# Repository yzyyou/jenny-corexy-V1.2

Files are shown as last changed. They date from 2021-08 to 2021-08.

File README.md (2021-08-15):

# jenny-corexy-V1.2
metallized structure inspire by vorondesign voron2.4 https://github.com/VoronDesign/Voron-2

Project Home  http://wiki.jenny3dprint.com/index.php?title=Jenny_corexy_voron_V1.2_mainpage
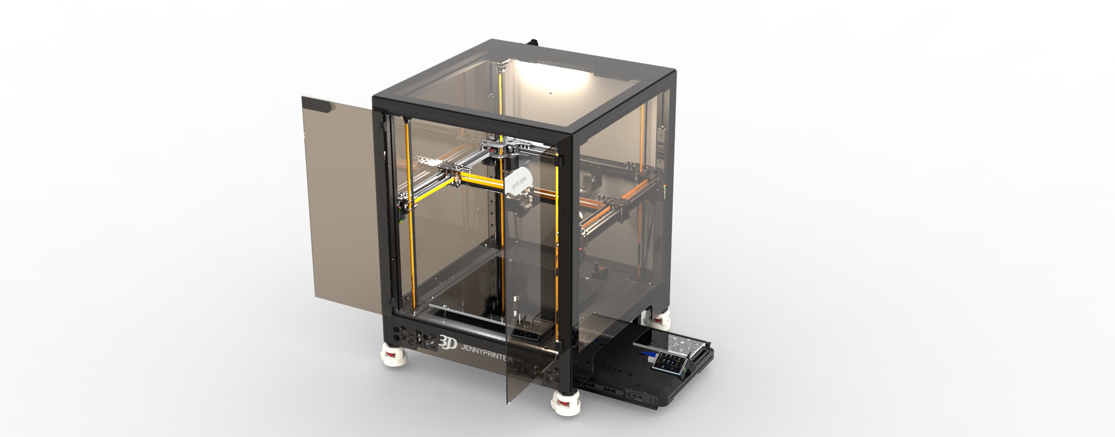
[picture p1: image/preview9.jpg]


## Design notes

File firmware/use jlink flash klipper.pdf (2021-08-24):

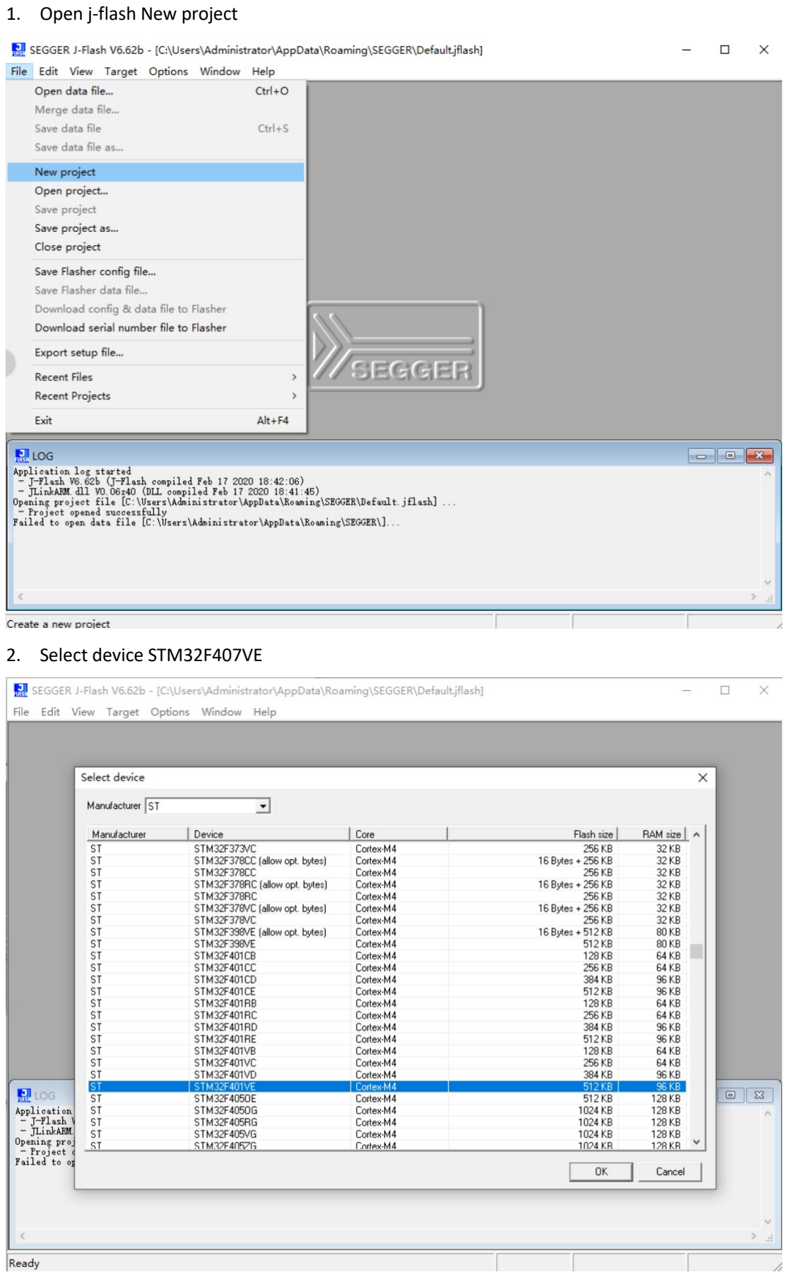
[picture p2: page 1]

### 1. Open j-flash New project

### 2. Select device STM32F407VE

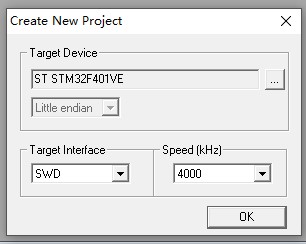
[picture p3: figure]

### 3. Open data file klipper.bin,start address use 0x8000000

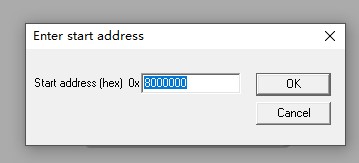
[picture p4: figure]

### 4. Use Jlink connect to MCU board’s SWDIO 、SWCLK 、GND、D+3V3

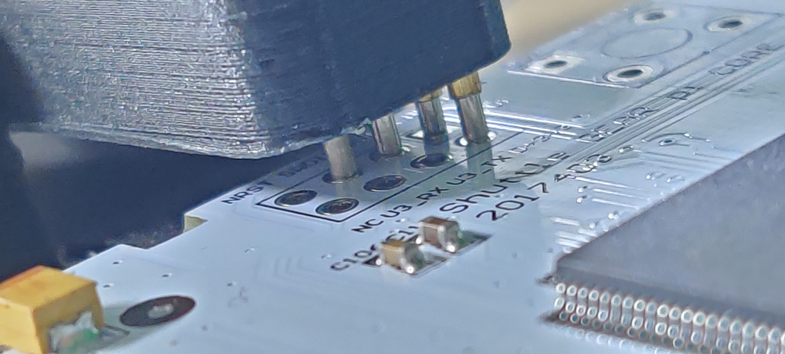
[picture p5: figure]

### 5. Click Target menu -> connect

### 6. Click Target menu -> Manua Programming -> Erase chip

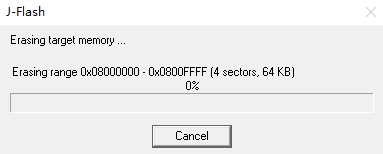
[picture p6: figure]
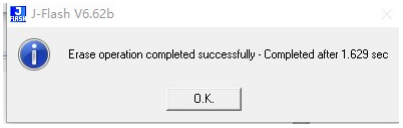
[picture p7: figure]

### 7. Click Target menu -> Manua Programming -> Program & Verify

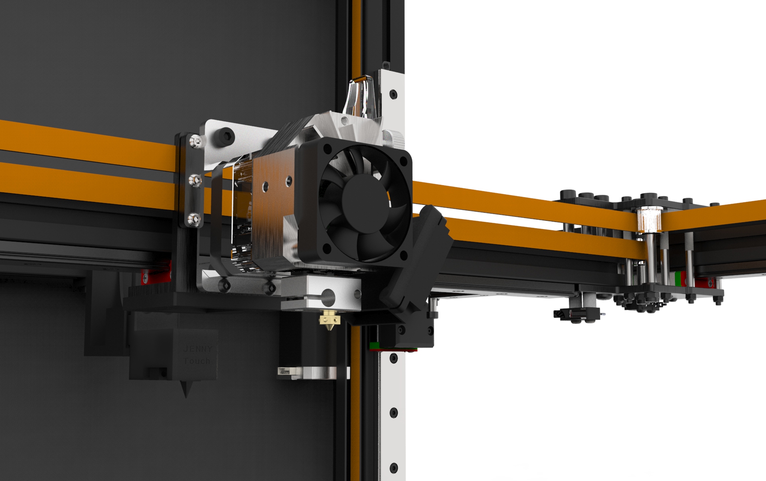
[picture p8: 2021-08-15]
image/preview7.jpg

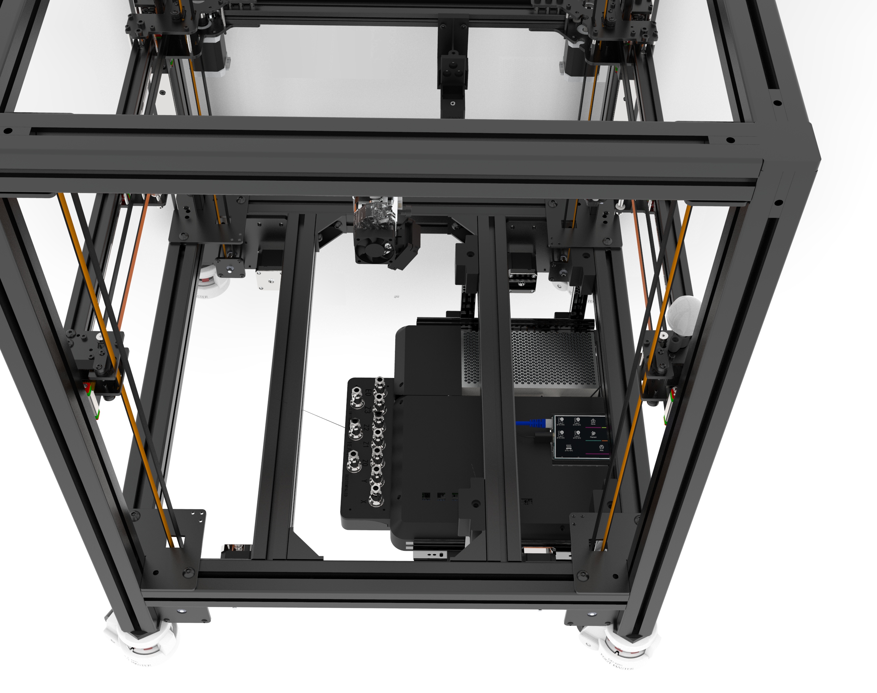
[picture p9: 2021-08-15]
image/preview3.jpg

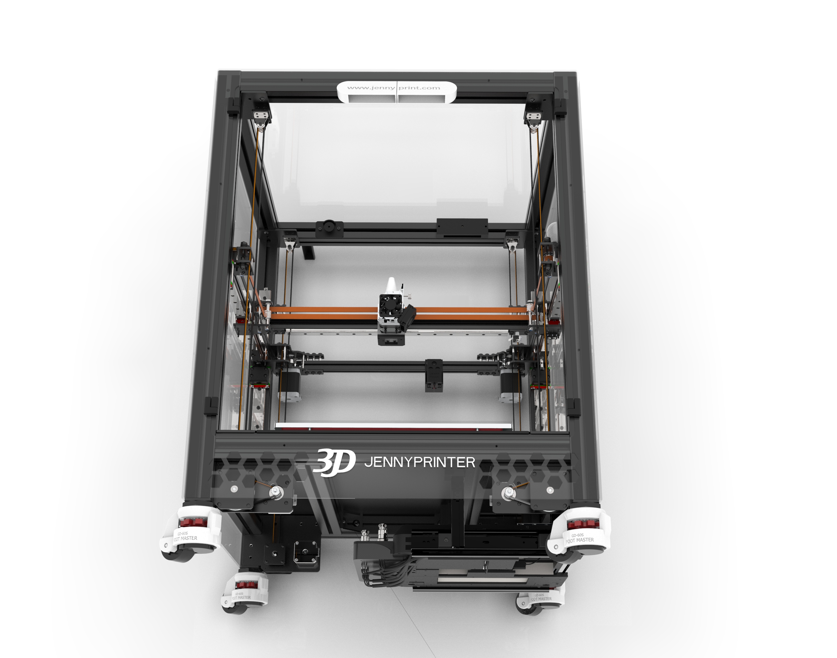
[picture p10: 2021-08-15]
image/preview4.jpg

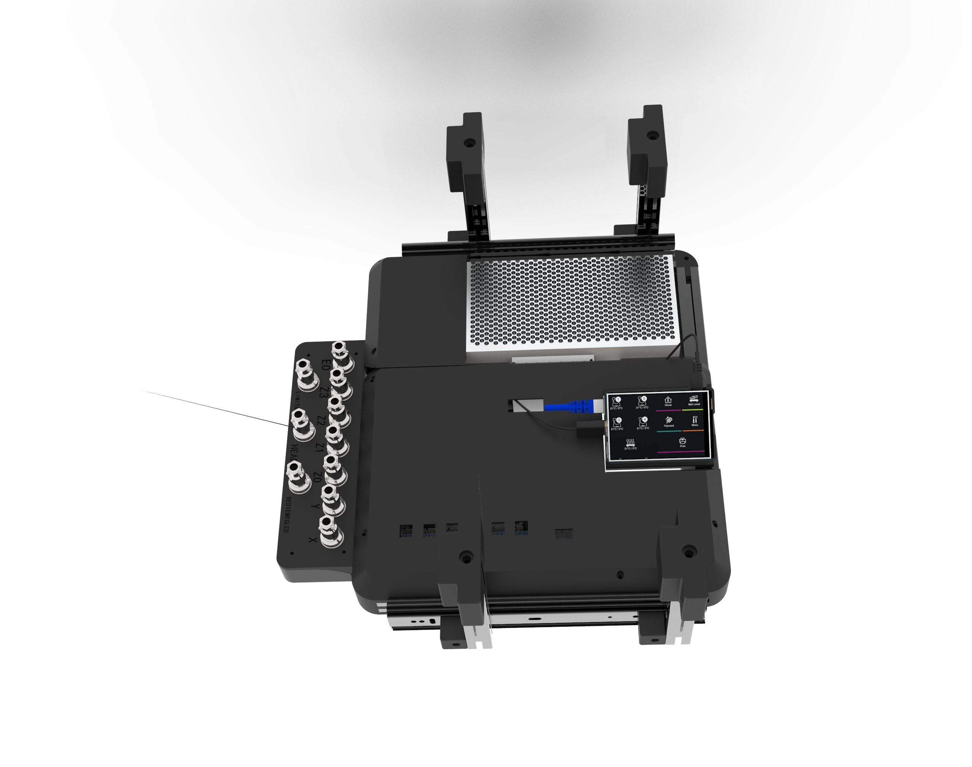
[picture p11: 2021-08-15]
image/preview8.jpg

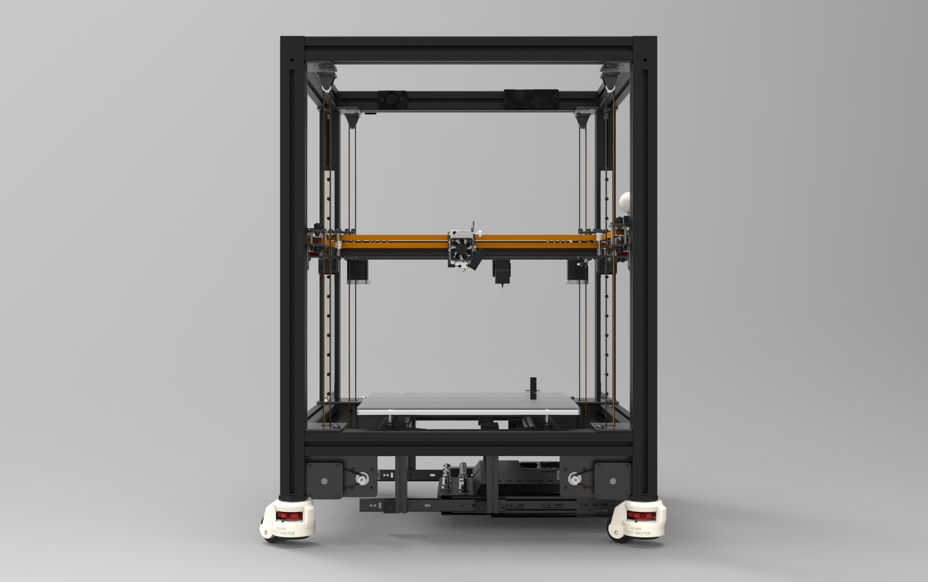
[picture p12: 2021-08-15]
image/preview2.jpg

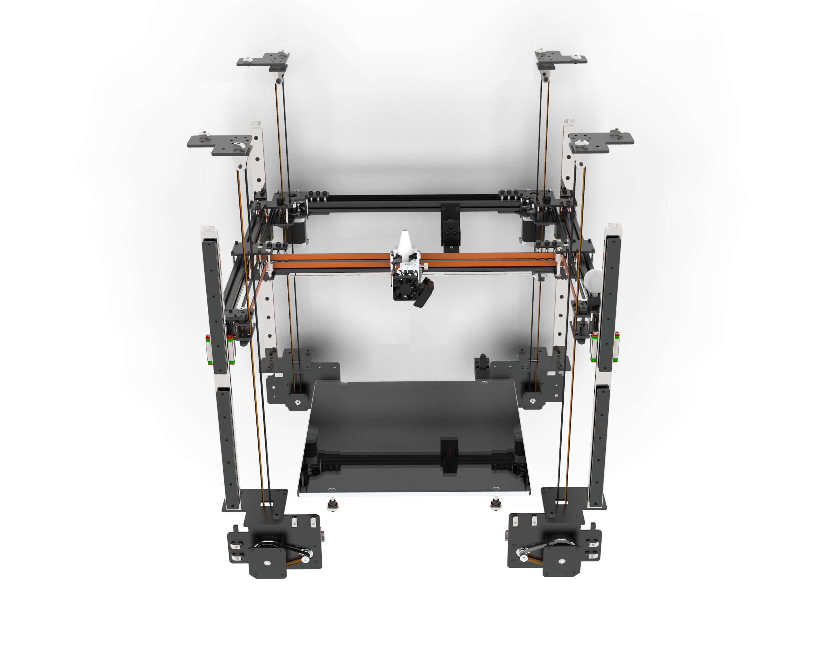
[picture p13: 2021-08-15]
image/preview6.jpg

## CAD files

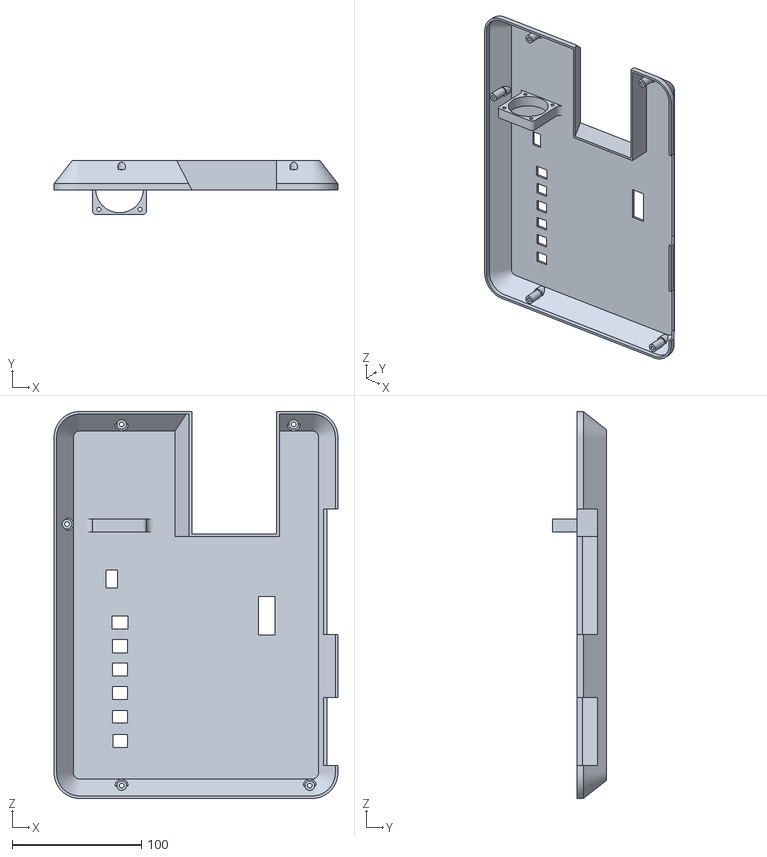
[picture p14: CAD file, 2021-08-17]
STLs/8_(optional)Main board cover plate.STL
220.0 x 42.0 x 300.0

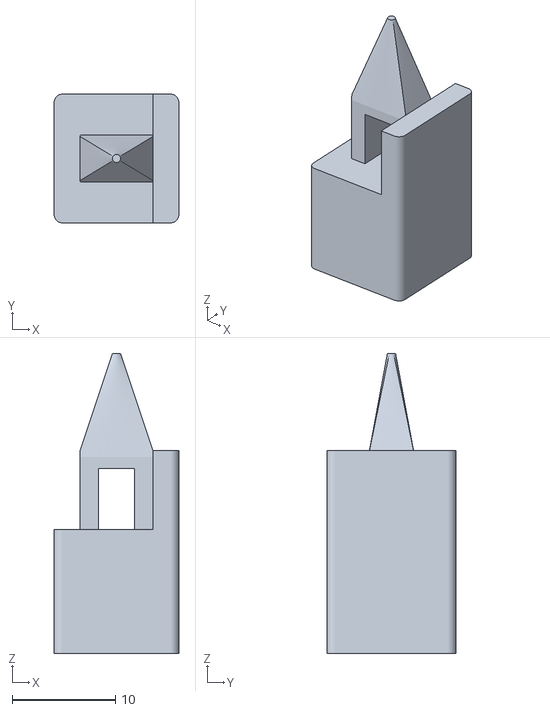
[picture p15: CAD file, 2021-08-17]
STLs/21_JennyTouch centre.STL
12.1 x 12.4 x 29.0

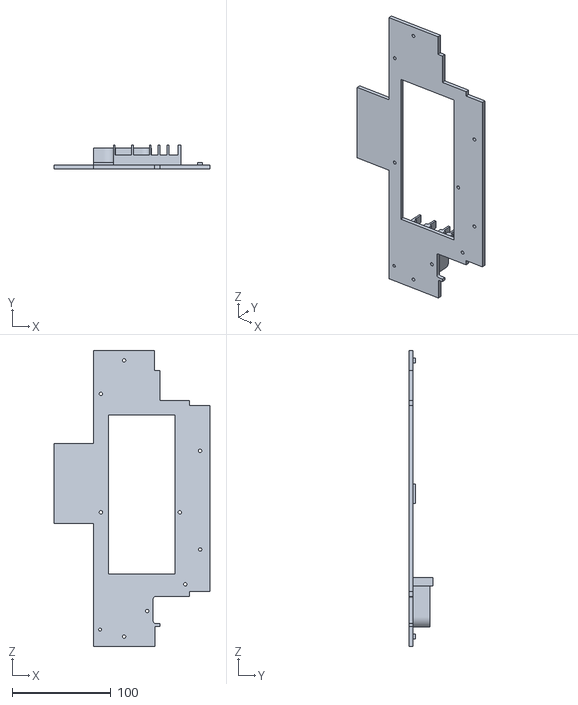
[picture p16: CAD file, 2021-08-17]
STLs/9_(optional)power bracket.STL
158.0 x 24.0 x 300.0

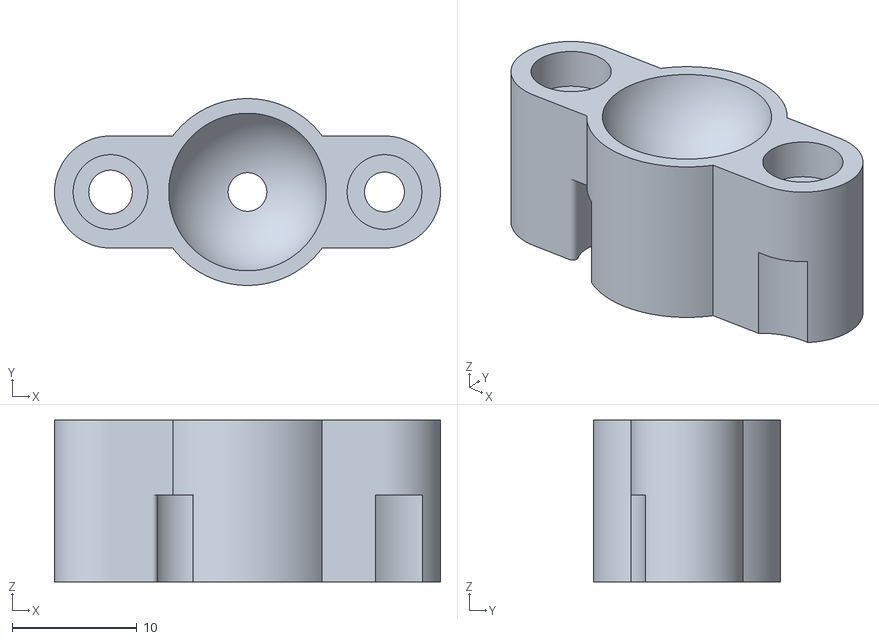
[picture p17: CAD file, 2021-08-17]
STLs/4_USB camera bracket.STL
31.0 x 15.0 x 13.0

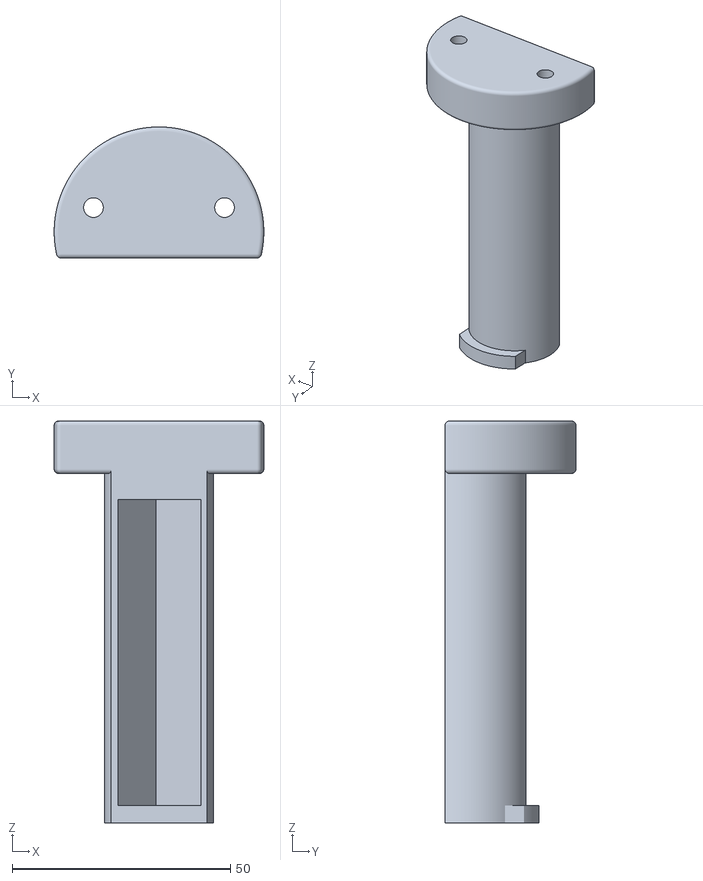
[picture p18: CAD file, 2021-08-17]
STLs/11_Filament hanging.STL
48.0 x 30.0 x 92.0

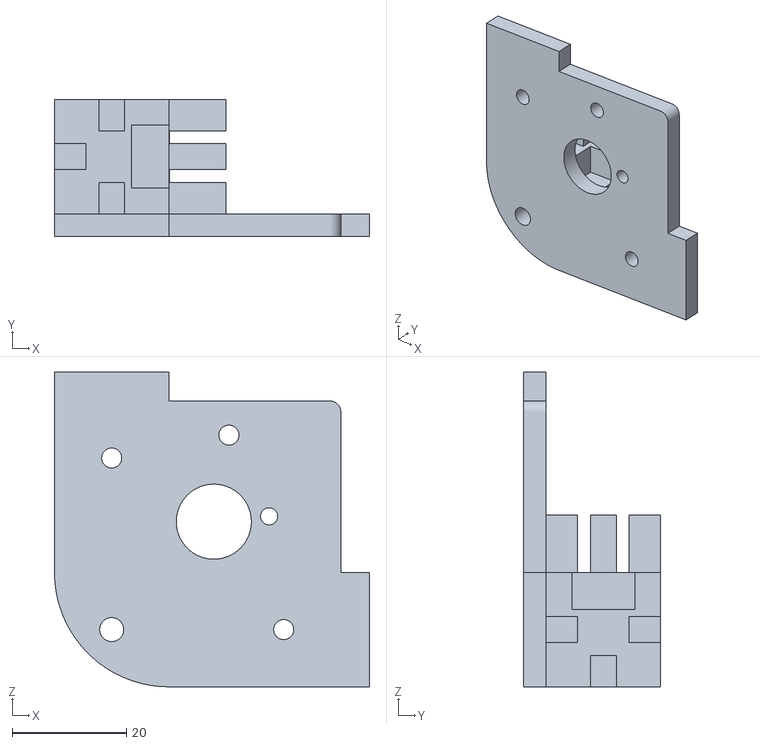
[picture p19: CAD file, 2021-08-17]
STLs/6_(optional)drawer cornerx4.STL
55.1 x 24.0 x 55.0

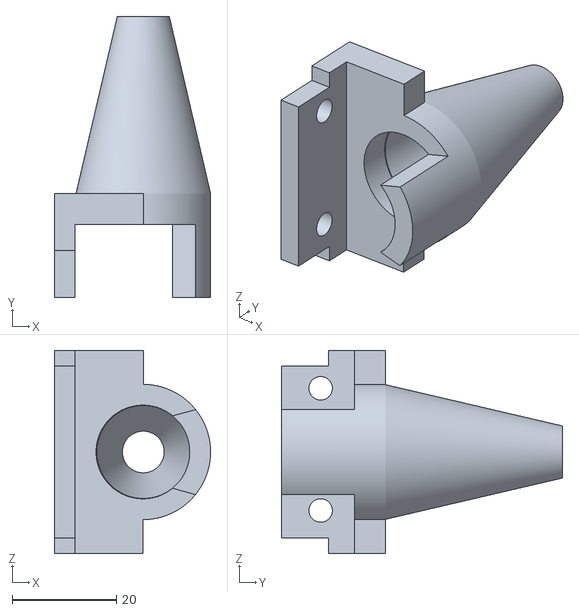
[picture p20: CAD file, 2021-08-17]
STLs/27_BMG Printhead wireTPU print.STL
30.0 x 54.0 x 39.0

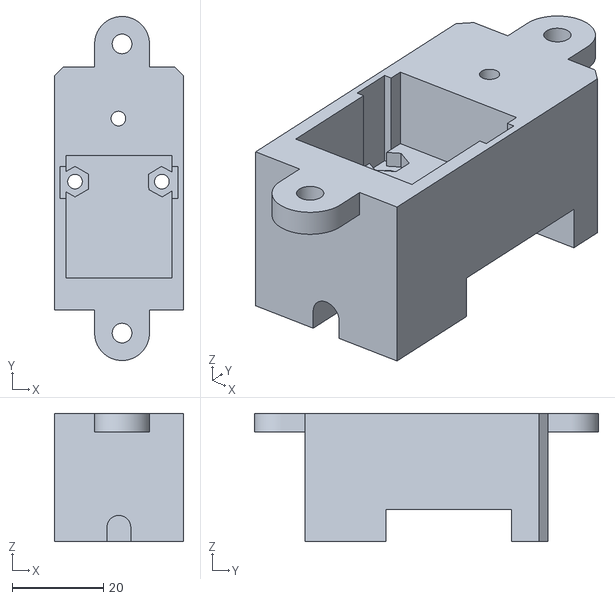
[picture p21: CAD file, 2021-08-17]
STLs/20_JennyLimitSwitch body.STL
28.3 x 75.2 x 28.0

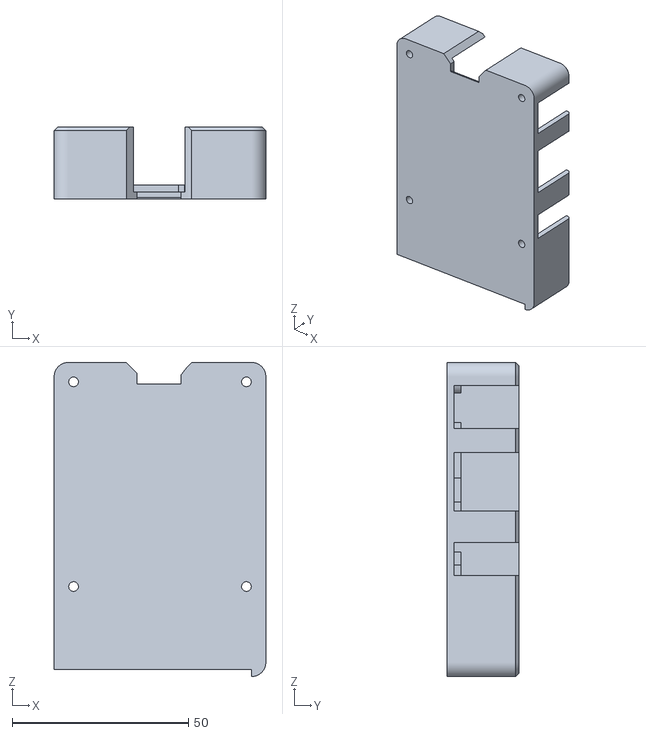
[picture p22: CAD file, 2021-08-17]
STLs/18_(optional)raspberry pi cover.STL
60.0 x 20.5 x 89.0

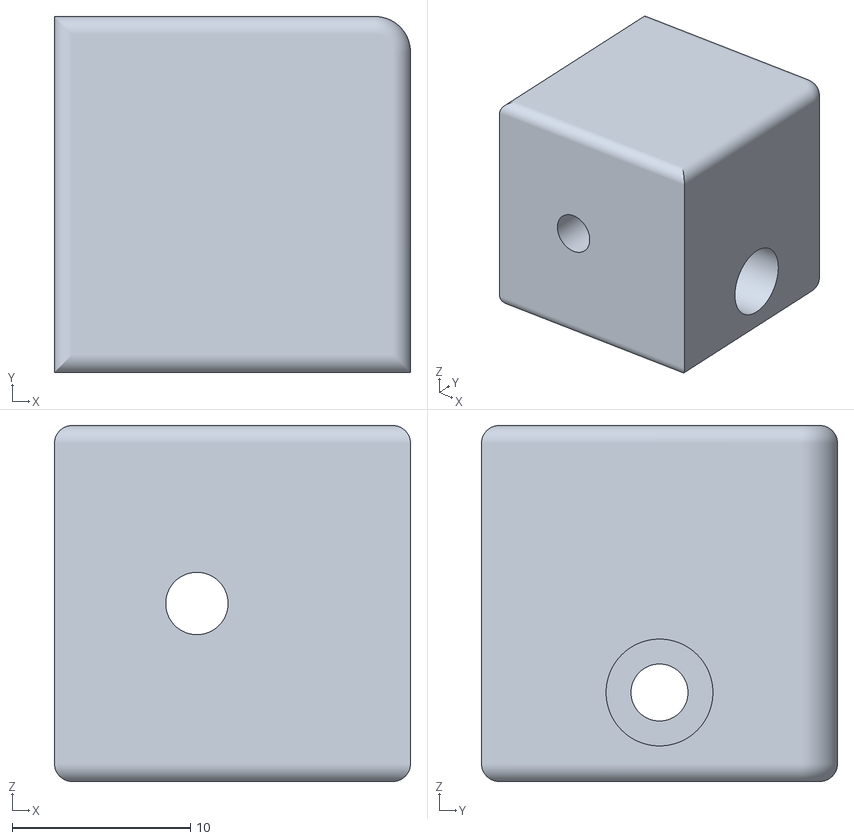
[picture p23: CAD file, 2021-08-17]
STLs/7_Drawer fixation cubex4.STL
20.0 x 20.0 x 20.0

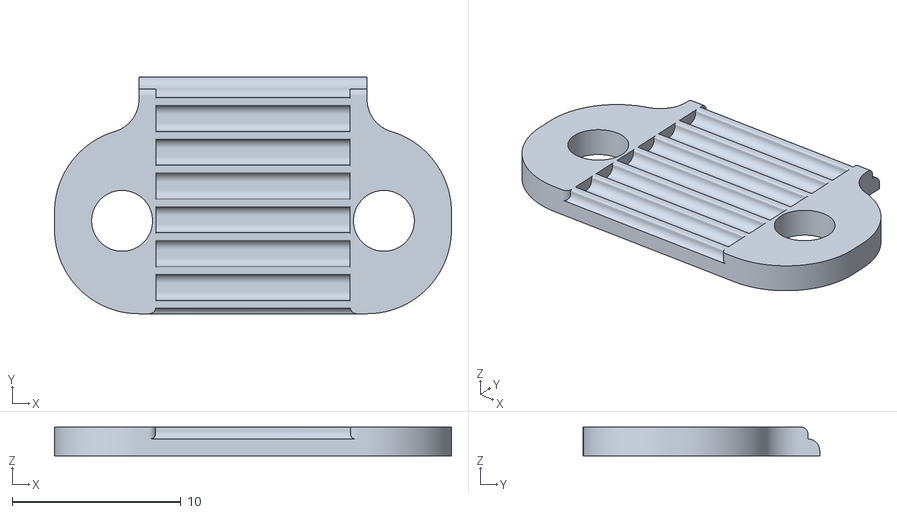
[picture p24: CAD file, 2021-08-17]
STLs/14_Z blet block bottom x8.STL
23.5 x 14.0 x 1.70

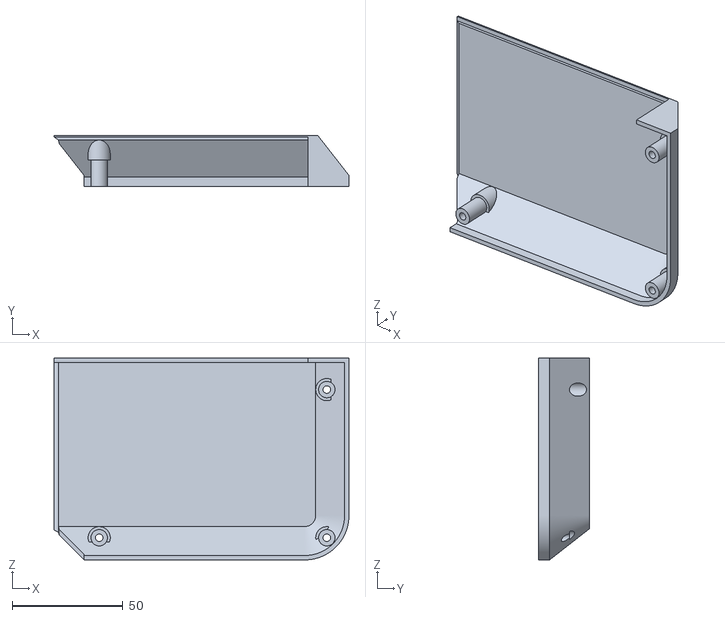
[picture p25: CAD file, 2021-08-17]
STLs/16_(optional)power cover.STL
133.0 x 23.0 x 91.0

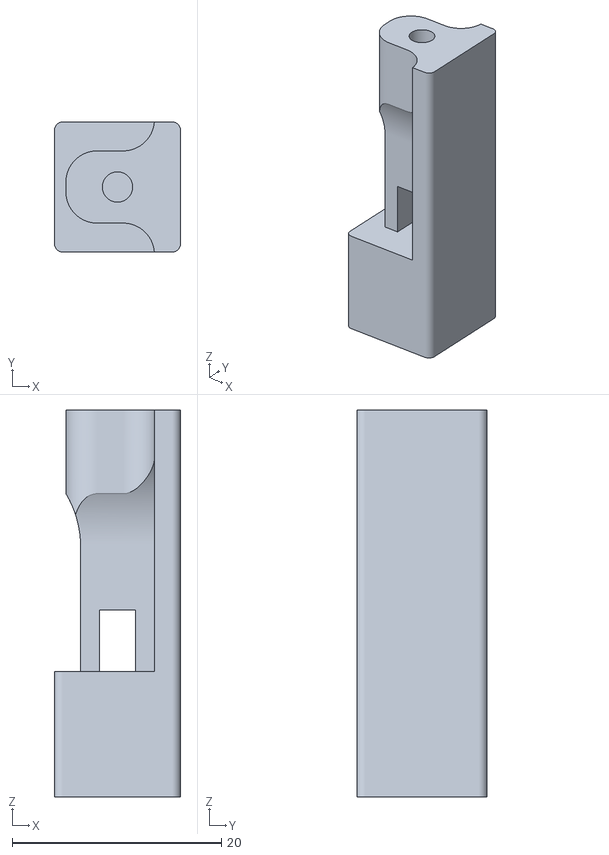
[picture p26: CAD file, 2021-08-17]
STLs/19_JennyLimitSwitch centre.STL
12.1 x 12.4 x 37.0

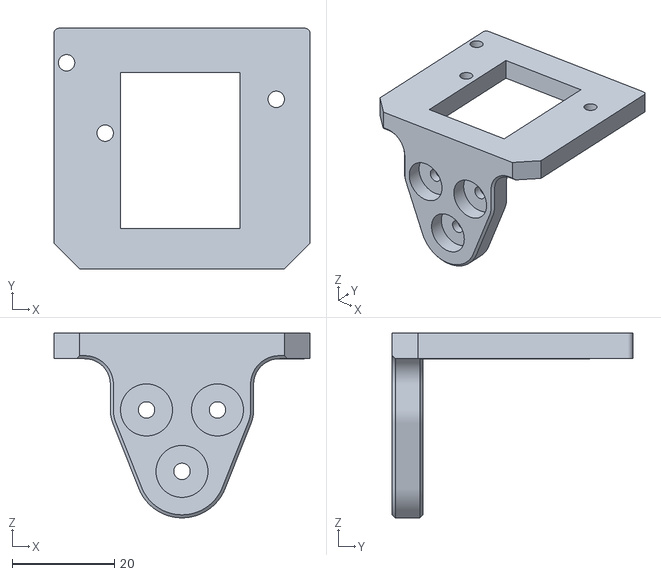
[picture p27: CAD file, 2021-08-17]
STLs/23_JennyTouch bracket.STL
50.0 x 47.0 x 36.1

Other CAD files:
Panels/jenny corexy Panels(350x350x400).dwg
Panels/jenny corexy Panels(410x410x400).dwg
STLs/3_(optional)ssr bracket.STL
STLs/1_Gantry linear rails blockx4.STL
STLs/10_printhed fan bracket.STL
STLs/12_(optional)aviation plug cover.STL
STLs/13_(optional)aviation plug bottom.STL
STLs/15_Z blet block top x8.STL
STLs/17_(optional)raspberry pi bracket.STL
STLs/1_(optional)Gantry linear rails block(standby)x4.STL
STLs/22_JennyTouch mount.STL
STLs/24_JennyTouch body.STL
STLs/26_printhead buckle.STL
STLs/2_(optional)SEMotherboard bracket.STL
STLs/5_ Drawer fixation doppx4.STL

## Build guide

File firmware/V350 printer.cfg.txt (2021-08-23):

[include kiauh_macros.cfg]
[mcu]
serial:  /dev/ttyUSB0
restart_method: command

#[menu __main __octoprint]
#type: disabled

[pause_resume]

[display_status]

[virtual_sdcard]
path: ~/gcode_files

[printer]
kinematics: corexy
max_velocity: 250
max_accel: 6000
#max_accel_to_decel : 7000
max_z_velocity: 60
max_z_accel: 600

[stepper_x]
step_pin: PB2
dir_pin: !PA0
enable_pin: !PE2
step_distance: 0.0125
endstop_pin: !PD12
position_endstop: 350
position_max: 350
homing_speed: 190
homing_retract_dist: 0

[stepper_y]
step_pin: PC14
dir_pin: !PE6
enable_pin: !PC15
step_distance: 0.0125
endstop_pin: !PA11
position_endstop: 350
position_max: 350
homing_speed: 190
homing_retract_dist: 0

## Z0 Stepper - Front Left
[stepper_z]
step_pin: PE5
dir_pin: !PE4
enable_pin: !PC13
step_distance: 0.00125
endstop_pin: !PE1
position_endstop: 3.9 #modfiy this when nozzle changed.more small more far.
position_max: 350
homing_speed: 20
position_min: -10.0
second_homing_speed: 3.0
homing_retract_dist: 3.0

##      Z1 Stepper - Rear Left
[stepper_z1]
step_pin: PA1
dir_pin: PB0
enable_pin: !PC5
step_distance: 0.00125

##      Z2 Stepper - Rear Right
[stepper_z2]
step_pin: PC4
dir_pin: !PE3
enable_pin: !PB1
step_distance: 0.00125

##      Z3 Stepper - Front Right
[stepper_z3]
step_pin: PB3 
dir_pin: PB4
enable_pin: !PB5
#step_distance: 0.0015625
step_distance: 0.00125

[extruder]
## STP -> step pin
step_pin: PE8
## FR -> dir pin
dir_pin: PE7
## ST -> enable pin
enable_pin: !PE9
#step_distance: .00194
step_distance: .0048
nozzle_diameter: 0.400
filament_diameter: 1.750
heater_pin: !PC6 # Heat0
sensor_pin:  PC0 # T1 Header
#sensor_type: PT100 INA826
sensor_type: EPCOS 100K B57560G104F
control: pid
#pid_Kp=17.186 pid_Ki=0.556 pid_Kd=132.761
pid_Kp: 23.034
pid_Ki: 0.704
pid_Kd: 188.3
min_temp: -20
max_temp: 350
max_extrude_cross_section:100
##      Try to keep pressure_advance below 1.0
pressure_advance: 0.046
##      Default is 0.040, leave stock
pressure_advance_smooth_time: 0.040
max_extrude_only_velocity:100
max_extrude_only_accel:3000

[verify_heater extruder]
#max_error: 120
#   The maximum "cumulative temperature error" before raising an
#   error. Smaller values result in stricter checking and larger
#   values allow for more time before an error is reported.
#   Specifically, the temperature is inspected once a second and if it
#   is close to the target temperature then an internal "error
#   counter" is reset; otherwise, if the temperature is below the
#   target range then the counter is increased by the amount the
#   reported temperature differs from that range. Should the counter
#   exceed this "max_error" then an error is raised. The default is
#   120.
#check_gain_time: 15
#   This controls heater verification during initial heating. Smaller
#   values result in stricter checking and larger values allow for
#   more time before an error is reported. Specifically, during
#   initial heating, as long as the heater increases in temperature
#   within this time frame (specified in seconds) then the internal
#   "error counter" is reset. The default is 20 seconds for extruders
#   and 60 seconds for heater_bed.
#hysteresis: 3
#   The maximum temperature difference (in Celsius) to a target
#   temperature that is considered in range of the target. This
#   controls the max_error range check. It is rare to customize this
#   value. The default is 5.
#heating_gain: 6
#   The minimum temperature (in Celsius) that the heater must increase
#   by during the check_gain_time check. It is rare to customize this
#   value. The default is 2.

[heater_bed]
heater_pin: !PB13
sensor_pin: PC1
##      Thermistor Types
##   "EPCOS 100K B57560G104F"
##   "ATC Semitec 104GT-2"
##   "NTC 100K beta 3950"
##   "Honeywell 100K 135-104LAG-J01"
##   "NTC 100K MGB18-104F39050L32" (Keenovo Heater Pad)
##   "AD595"
##   "PT100 INA826"
sensor_type: EPCOS 100K B57560G104F
control: watermark
min_temp: 0
max_temp: 120

[probe]
pin: PC8
x_offset: 0
y_offset: 25.0
z_offset: 0
speed: 10.0
samples: 2
samples_result: average
sample_retract_dist: 3.0
samples_tolerance: 0.05
samples_tolerance_retries: 3

[fan]
pin: !PB6
kick_start_time: 0.5
off_below: 0.10
cycle_time: 0.001

[heater_fan fan1]
pin: !PB8
max_power: 1.0
kick_start_time: 0.5
heater: extruder
heater_temp: 50.0

[heater_fan controller_fan]
pin: !PB9
kick_start_time: 0.500
heater: heater_bed
heater_temp: 45.0

#[heater_fan exhaust_fan]
#pin: z:P2.7
#max_power: 1.0
#shutdown_speed: 0.0
#kick_start_time: 5.0
#heater: heater_bed
#heater_temp: 60
#fan_speed: 1.0

#[heater_fan fan2]
#pin: PE6

[skew_correction]

#[idle_timeout]
#timeout: 1800

[force_move]
enable_force_move: true
#   Set to true to enable FORCE_MOVE and SET_KINEMATIC_POSITION
#   extended G-Code commands. The default is false.

[homing_override]
axes: z
set_position_z: 0
gcode:
   SET_PIN PIN=Z_ENABLE VALUE=100
   G90
   G0 Z50 F1200
   G28 X Y 
   G0 X280 Y320 F4800
   G28 Z
   G0 Z50 F1200
   G0 X240  F4800

[quad_gantry_level]
gantry_corners:
        -60,-10
        340,360
#       Probe points
points:
	10,10
	10,270
	310,270
        310,10	
speed: 80
horizontal_move_z:35
retries: 5
retry_tolerance: 0.04
max_adjust: 90

#####################################################################
#       Macros
#####################################################################
[output_pin case_light]
pin: !PA3
pwm: true
shutdown_value: 0
cycle_time: 0.01
scale: 255

[output_pin Z_ENABLE]
pin: !PC7
pwm: true
shutdown_value: 0
cycle_time: 0.01
scale: 100

[gcode_button POWER_OFF_KEY]
pin:PA15
press_gcode:
        SET_PIN PIN=POWER_OFF VALUE=100

[output_pin POWER_OFF]
#pin: !PA15
pin: !PB12
pwm: true
shutdown_value: 0
cycle_time: 0.01
scale: 100

[gcode_macro M355]
variable_light_before: 0
default_parameter_S: 0
default_parameter_P: 0
gcode:
        SET_PIN PIN=case_light VALUE={S|float * P|float}

[gcode_macro ENDSTOPS_PROBE_STATUS]
gcode:
        QUERY_ENDSTOPS
        QUERY_PROBE

[gcode_macro TEST_X]
gcode:        
        STEPPER_BUZZ STEPPER=stepper_x 

[gcode_macro TEST_Y]
gcode:        
        STEPPER_BUZZ STEPPER=stepper_y 

[gcode_macro TEST_Z0]
gcode:   
        STEPPER_BUZZ STEPPER=stepper_z

[gcode_macro TEST_Z1]
gcode:   
        STEPPER_BUZZ STEPPER=stepper_z1

[gcode_macro TEST_Z2]
gcode:   
        STEPPER_BUZZ STEPPER=stepper_z2

[gcode_macro TEST_Z3]
gcode:   
        STEPPER_BUZZ STEPPER=stepper_z3

[gcode_macro LIGHT_ON]
gcode:
        M355 S1 P255

[gcode_macro LIGHT_OFF]
gcode:
        M355 S0 P0

[gcode_macro MOUNT_PROBE]
gcode:
        G1 X220 Y300 F3600;
        G1 X220 Y350 F3600;
        G1 X180 Y350 F3600;
        G1 X180 Y300 F3600;

[gcode_macro UMOUNT_PROBE]
gcode:
        G1 X180 Y300 F3600;
        G1 X180 Y350 F3600;
        G1 X220 Y350 F3600;
        G1 X220 Y300 F3600;

[gcode_macro UNLOCK_Z_MOVE]
gcode:
        SET_PIN PIN=Z_ENABLE VALUE=100

[gcode_macro ENABLE_Z_MOVE]
gcode:        
        SET_STEPPER_ENABLE STEPPER=stepper_z ENABLE=1
        SET_STEPPER_ENABLE STEPPER=stepper_z1 ENABLE=1
        SET_STEPPER_ENABLE STEPPER=stepper_z2 ENABLE=1
        SET_STEPPER_ENABLE STEPPER=stepper_z3 ENABLE=1
        SET_PIN PIN=Z_ENABLE VALUE=100

[gcode_macro FORCE_POWER_OFF]
gcode:
        SET_PIN PIN=POWER_OFF VALUE=100

[gcode_macro G32]
gcode:
    #BED_MESH_CLEAR
    G28
    MOUNT_PROBE
    QUAD_GANTRY_LEVEL
    UMOUNT_PROBE
    G28
    G0 X250 Y250 Z20 F1200

[gcode_macro POWER_LOSS]
description: in the actual running print power loss happen
gcode:
    
    SET_PIN PIN=case_light VALUE=0.00 SAVE=0
    #SET_FAN_SPEED controller_fan=0
    #SET_FAN_SPEED fan=0
    #SET_FAN_SPEED fan1=0
    M106 S0
    #################
    ##### set defaults #####
    #{% set x = params.X|default(230) %}      #edit to your park position
    #{% set y = params.Y|default(230) %}      #edit to your park position
    #{% set z = params.Z|default(10)|float %} #edit to your park position
    #{% set e = params.E|default(1) %}        #edit to your retract length
    ##### calculate save lift position #####
  
    #{%set min_extrude_temp = printer.configfile.settings["extruder"]["min_extrude_temp"]|int %}
    #{%set act_extrude_temp = printer.extruder.temperature|int %}
    
    #SAVE_GCODE_STATE NAME=PAUSE_state

    PAUSE
    TURN_OFF_HEATERS
    ##### end of definitions #####

    M117 unexpected power off happened

[gcode_macro PRINT_START]
#   Use PRINT_START for the slicer starting script - please customise for your slicer of choice
gcode:
    SET_SKEW XY=140.6,140.8,99.94
    #G28                            ; home all axes
    G32
    G1 Z20 F3000                   ; move nozzle away from bed
    G1 X30 Y0 Z0.3 F3000
    G92 E0
    G1 X40 E20 F100
    G1 X50 F2100
    G92 E0

[gcode_macro PRINT_END]
#   Use PRINT_END for the slicer ending script - please customise for your slicer of choice
gcode:
    M400                           ; wait for buffer to clear
    G92 E0                         ; zero the extruder
    G1 E-10.0 F3600                ; retract filament
    G91                            ; relative positioning
    G0 Z1.00 X20.0 Y25.0 F20000    ; move nozzle to remove stringing
    TURN_OFF_HEATERS
    M107                           ; turn off fan
    G1 Z2 F3000                    ; move nozzle up 2mm
    G90                            ; absolute positioning
    G0  X125 Y250 F3600            ; park nozzle at rear
    SET_SKEW CLEAR=1

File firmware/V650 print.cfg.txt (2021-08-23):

[include kiauh_macros.cfg]
[mcu]
serial:  /dev/ttyUSB0
restart_method: command

#[menu __main __octoprint]
#type: disabled

#[mcu rpi]
#serial: /tmp/klipper_host_mcu

#[adxl345]
#cs_pin: rpi:gpio11

#[resonance_tester]
#accel_chip: adxl345
#probe_points:
#    325,325,20  # middle of print bed

[pause_resume]

[display_status]

[virtual_sdcard]
path: ~/gcode_files

[printer]
kinematics: corexy
max_velocity: 260
max_accel:6000
#max_accel_to_decel:7000
max_z_velocity: 10
max_z_accel: 100

[stepper_x]
step_pin: PB2
dir_pin: !PA0
enable_pin: !PE2
step_distance: 0.0125
endstop_pin: PA11
position_endstop: 650
position_max: 650
homing_speed: 100
homing_retract_dist: 0

[stepper_y]
step_pin: PC14
dir_pin: !PE6
enable_pin: !PC15
step_distance: 0.0125
endstop_pin: PD12
position_endstop: 650
position_max: 650
homing_speed: 100
homing_retract_dist: 0

## Z0 Stepper - Front Left
[stepper_z]
step_pin: PE5
dir_pin: PE4
enable_pin: !PC13
step_distance: 0.0025
endstop_pin: PE0
position_endstop: 12.7 #modfiy this when nozzle changed.more small more far.
position_max: 512
homing_speed: 15
position_min: -10
second_homing_speed: 3.0
homing_retract_dist: 3.0

##      Z1 Stepper - Rear Left
[stepper_z1]
step_pin: PA1
dir_pin: !PB0
enable_pin: !PC5
step_distance: 0.0025

##      Z2 Stepper - Rear Right
[stepper_z2]
step_pin: PC4
dir_pin: PE3
enable_pin: !PB1
step_distance: 0.0025

##      Z3 Stepper - Front Right
[stepper_z3]
step_pin: PB3
dir_pin: !PB4
enable_pin: !PB5
#step_distance: 0.0015625
step_distance: 0.0025

[extruder]
step_pin: PE8
dir_pin: PE7
enable_pin: !PE9
#step_distance: .00194
step_distance: .0048
nozzle_diameter: 0.400
filament_diameter: 1.750
heater_pin: !PC6 # Heat0
sensor_pin:  PC0 # T1 Header
#sensor_type: PT100 INA826
sensor_type: EPCOS 100K B57560G104F
control: pid
#pid_Kp=17.186 pid_Ki=0.556 pid_Kd=132.761
#pid_Kp: 22.2
#pid_Ki: 1.08
#pid_Kd: 114
pid_Kp=18.731
pid_Ki=0.827 
pid_Kd=106.065 

min_temp: -20
max_temp: 350
max_extrude_cross_section:100
##      Try to keep pressure_advance below 1.0
pressure_advance: 0.046
##      Default is 0.040, leave stock
pressure_advance_smooth_time: 0.040
max_extrude_only_velocity:100
max_extrude_only_accel:3000

[verify_heater extruder]
#max_error: 120
#   The maximum "cumulative temperature error" before raising an
#   error. Smaller values result in stricter checking and larger
#   values allow for more time before an error is reported.
#   Specifically, the temperature is inspected once a second and if it
#   is close to the target temperature then an internal "error
#   counter" is reset; otherwise, if the temperature is below the
#   target range then the counter is increased by the amount the
#   reported temperature differs from that range. Should the counter
#   exceed this "max_error" then an error is raised. The default is
#   120.
#check_gain_time: 15
#   This controls heater verification during initial heating. Smaller
#   values result in stricter checking and larger values allow for
#   more time before an error is reported. Specifically, during
#   initial heating, as long as the heater increases in temperature
#   within this time frame (specified in seconds) then the internal
#   "error counter" is reset. The default is 20 seconds for extruders
#   and 60 seconds for heater_bed.
#hysteresis: 3
#   The maximum temperature difference (in Celsius) to a target
#   temperature that is considered in range of the target. This
#   controls the max_error range check. It is rare to customize this
#   value. The default is 5.
#heating_gain: 6
#   The minimum temperature (in Celsius) that the heater must increase
#   by during the check_gain_time check. It is rare to customize this
#   value. The default is 2.

[heater_bed]
heater_pin: !PB13
sensor_pin: PC1
##      Thermistor Types
##   "EPCOS 100K B57560G104F"
##   "ATC Semitec 104GT-2"
##   "NTC 100K beta 3950"
##   "Honeywell 100K 135-104LAG-J01"
##   "NTC 100K MGB18-104F39050L32" (Keenovo Heater Pad)
##   "AD595"
##   "PT100 INA826"
sensor_type: EPCOS 100K B57560G104F
control: watermark
min_temp: 0
max_temp: 120

[probe]
pin: PC8
x_offset: 0
y_offset: 25.0
z_offset: 0
speed: 30.0
samples: 2
samples_result: average
sample_retract_dist: 3.0
samples_tolerance: 0.05
samples_tolerance_retries: 3

[fan]
pin: !PB8
kick_start_time: 0.5
off_below: 0.10
cycle_time: 0.001

[heater_fan fan1]
pin: !PB6
max_power: 1.0
kick_start_time: 0.5
heater: extruder
heater_temp: 50.0

[heater_fan controller_fan]
pin: !PB9
kick_start_time: 0.500
heater: heater_bed
heater_temp: 45.0

#[heater_fan exhaust_fan]
#pin: z:P2.7
#max_power: 1.0
#shutdown_speed: 0.0
#kick_start_time: 5.0
#heater: heater_bed
#heater_temp: 60
#fan_speed: 1.0

#[heater_fan fan2]
#pin: PE6

[skew_correction]
#SET_SKEW XY=140.5,140.1,99.92

#[idle_timeout]
#timeout: 1800

[force_move]
enable_force_move: true
#   Set to true to enable FORCE_MOVE and SET_KINEMATIC_POSITION
#   extended G-Code commands. The default is false.

[homing_override]
axes: z
set_position_z: 0
gcode:
   SET_PIN PIN=Z_ENABLE VALUE=100
   G90
   G0 Z50 F1200
   G28 X Y
   G0 X590 Y648  F4800
   G28 Z
   G0 Z50 F1200
   G0 X550  F4800

[quad_gantry_level]
gantry_corners:
        -60,-10
        750,800
#       Probe points
points:
        30,20
        30,560
        620,560
        620,20
speed: 100
horizontal_move_z: 50
retries: 5
retry_tolerance: 0.05
max_adjust: 90

#####################################################################
#       Macros
#####################################################################
[output_pin case_light]
pin: !PA3
pwm: true
shutdown_value: 0
cycle_time: 0.01
scale: 255

[output_pin Z_ENABLE]
pin: !PC7
pwm: true
shutdown_value: 0
cycle_time: 0.01
scale: 100

[gcode_button POWER_OFF_KEY]
pin:PA15
press_gcode:
        SET_PIN PIN=POWER_OFF VALUE=100

[output_pin POWER_OFF]
#pin: !PA15
pin: !PB12
pwm: true
shutdown_value: 0
cycle_time: 0.01
scale: 100

[gcode_macro M355]
variable_light_before: 0
default_parameter_S: 0
default_parameter_P: 0
gcode:
        SET_PIN PIN=case_light VALUE={S|float * P|float}

[gcode_macro ENDSTOPS_PROBE_STATUS]
gcode:
        QUERY_ENDSTOPS
        QUERY_PROBE

[gcode_macro TEST_X]
gcode:        
        STEPPER_BUZZ STEPPER=stepper_x 

[gcode_macro TEST_Y]
gcode:        
        STEPPER_BUZZ STEPPER=stepper_y 

[gcode_macro TEST_Z0]
gcode:   
        STEPPER_BUZZ STEPPER=stepper_z

[gcode_macro TEST_Z1]
gcode:   
        STEPPER_BUZZ STEPPER=stepper_z1

[gcode_macro TEST_Z2]
gcode:   
        STEPPER_BUZZ STEPPER=stepper_z2

[gcode_macro TEST_Z3]
gcode:   
        STEPPER_BUZZ STEPPER=stepper_z3

[gcode_macro LIGHT_ON]
gcode:
        M355 S1 P255

[gcode_macro LIGHT_OFF]
gcode:
        M355 S0 P0

[gcode_macro MOUNT_PROBE]
gcode:
        G1 X473 Y597 F3600;
        G1 X473 Y649 F3600;
        G1 X434 Y649 F3600;
        G1 X434 Y597 F3600;

[gcode_macro UMOUNT_PROBE]
gcode:
        G1 X434 Y597 F3600;
        G1 X434 Y647 F3600;
        G1 X473 Y647 F3600;
        G1 X473 Y597 F3600;

[gcode_macro UNLOCK_Z_MOVE]
gcode:
        SET_PIN PIN=Z_ENABLE VALUE=100

[gcode_macro ENABLE_Z_MOVE]
gcode:        
        SET_STEPPER_ENABLE STEPPER=stepper_z ENABLE=1
        SET_STEPPER_ENABLE STEPPER=stepper_z1 ENABLE=1
        SET_STEPPER_ENABLE STEPPER=stepper_z2 ENABLE=1
        SET_STEPPER_ENABLE STEPPER=stepper_z3 ENABLE=1
        SET_PIN PIN=Z_ENABLE VALUE=100

[gcode_macro FORCE_POWER_OFF]
gcode:
        SET_PIN PIN=POWER_OFF VALUE=100

[gcode_macro G32]
gcode:
    #BED_MESH_CLEAR
    G28
    MOUNT_PROBE
    QUAD_GANTRY_LEVEL
    UMOUNT_PROBE
    G28
    G0 X250 Y250 Z20 F1200

[gcode_macro POWER_LOSS]
description: in the actual running print power loss happen
gcode:
    
    SET_PIN PIN=case_light VALUE=0.00 SAVE=0
    #SET_FAN_SPEED controller_fan=0
    #SET_FAN_SPEED fan=0
    #SET_FAN_SPEED fan1=0
    M106 S0
    #################
    ##### set defaults #####
    #{% set x = params.X|default(230) %}      #edit to your park position
    #{% set y = params.Y|default(230) %}      #edit to your park position
    #{% set z = params.Z|default(10)|float %} #edit to your park position
    #{% set e = params.E|default(1) %}        #edit to your retract length
    ##### calculate save lift position #####
  
    #{%set min_extrude_temp = printer.configfile.settings["extruder"]["min_extrude_temp"]|int %}
    #{%set act_extrude_temp = printer.extruder.temperature|int %}
    
    #SAVE_GCODE_STATE NAME=PAUSE_state

    PAUSE
    TURN_OFF_HEATERS
    ##### end of definitions #####

    M117 unexpected power off happened

[gcode_macro PRINT_START]
#   Use PRINT_START for the slicer starting script - please customise for your slicer of choice
gcode:
    #G28                            ; home all axes
    SET_SKEW XY=140.5,140.1,99.92
    G32
    G1 Z20 F1200                   ; move nozzle away from bed
    G1 X30 Y10 Z0.3 F3600
    G92 E0
    G1 X40 E20 F100
    G1 X50 F2100
    G92 E0

[gcode_macro PRINT_END]
#   Use PRINT_END for the slicer ending script - please customise for your slicer of choice
gcode:
    M400                           ; wait for buffer to clear
    G92 E0                         ; zero the extruder
    G1 E-10.0 F3600                ; retract filament
    G91                            ; relative positioning
    G0 Z1.00 X20.0 Y25.0 F20000    ; move nozzle to remove stringing
    TURN_OFF_HEATERS
    M107                           ; turn off fan
    G1 Z8 F3000                    ; move nozzle up 2mm
    G90                            ; absolute positioning
    G0  X125 Y250 F3600            ; park nozzle at rear
    SET_SKEW CLEAR=1

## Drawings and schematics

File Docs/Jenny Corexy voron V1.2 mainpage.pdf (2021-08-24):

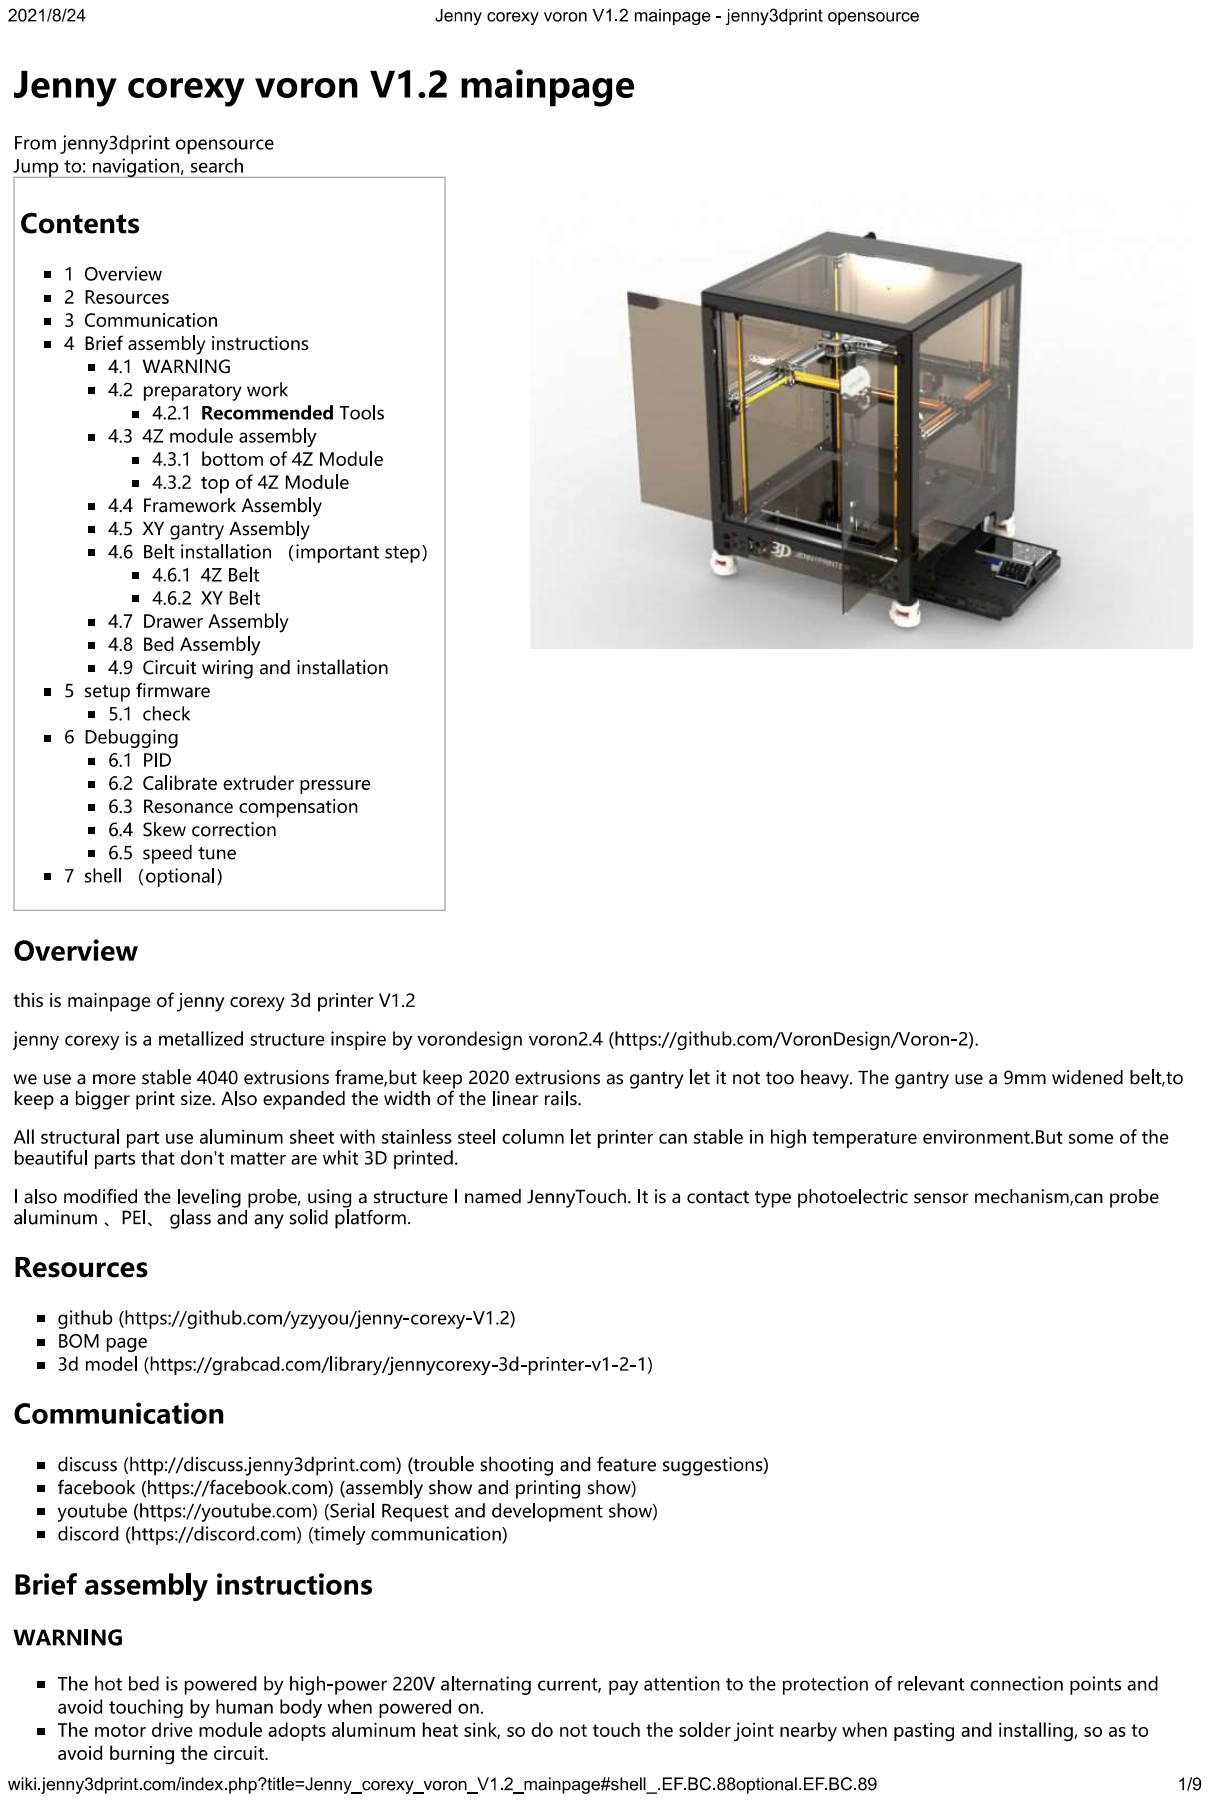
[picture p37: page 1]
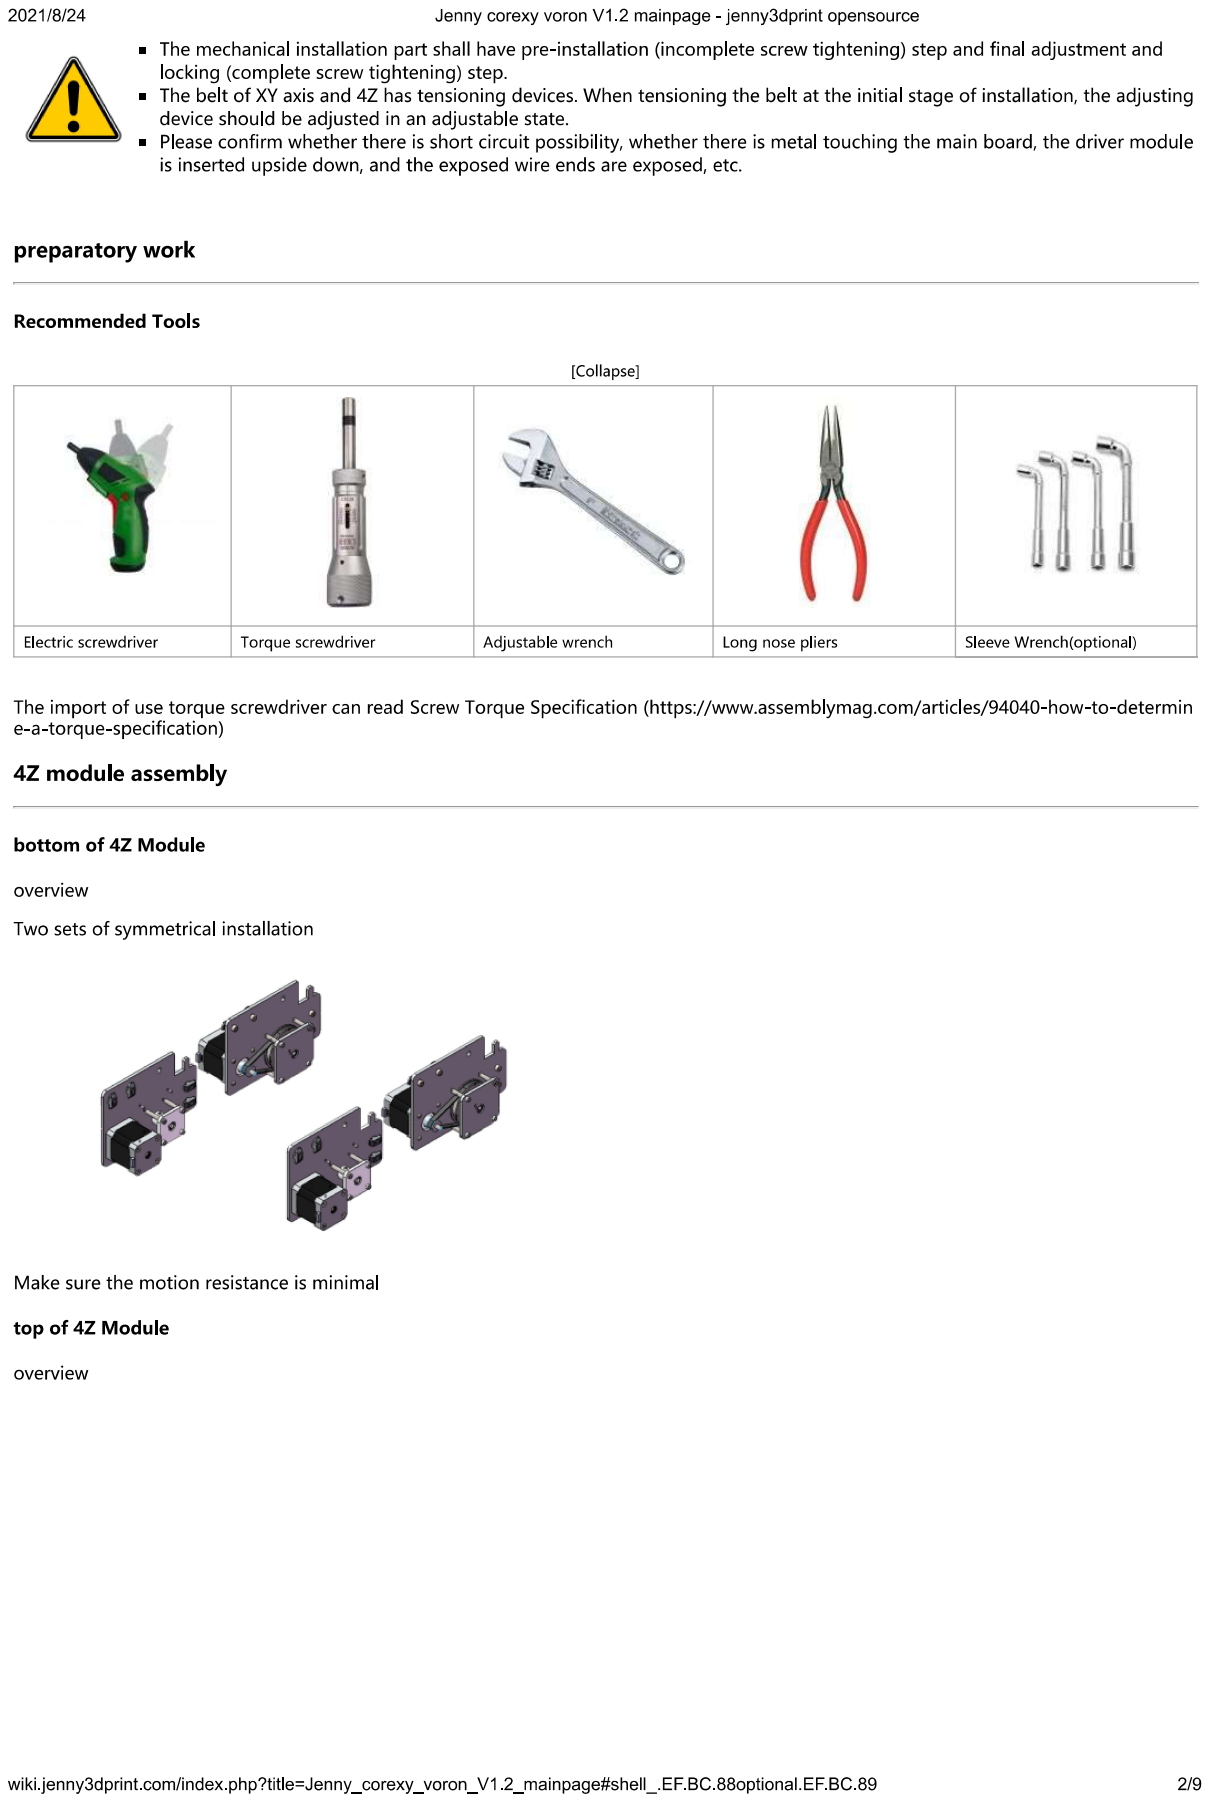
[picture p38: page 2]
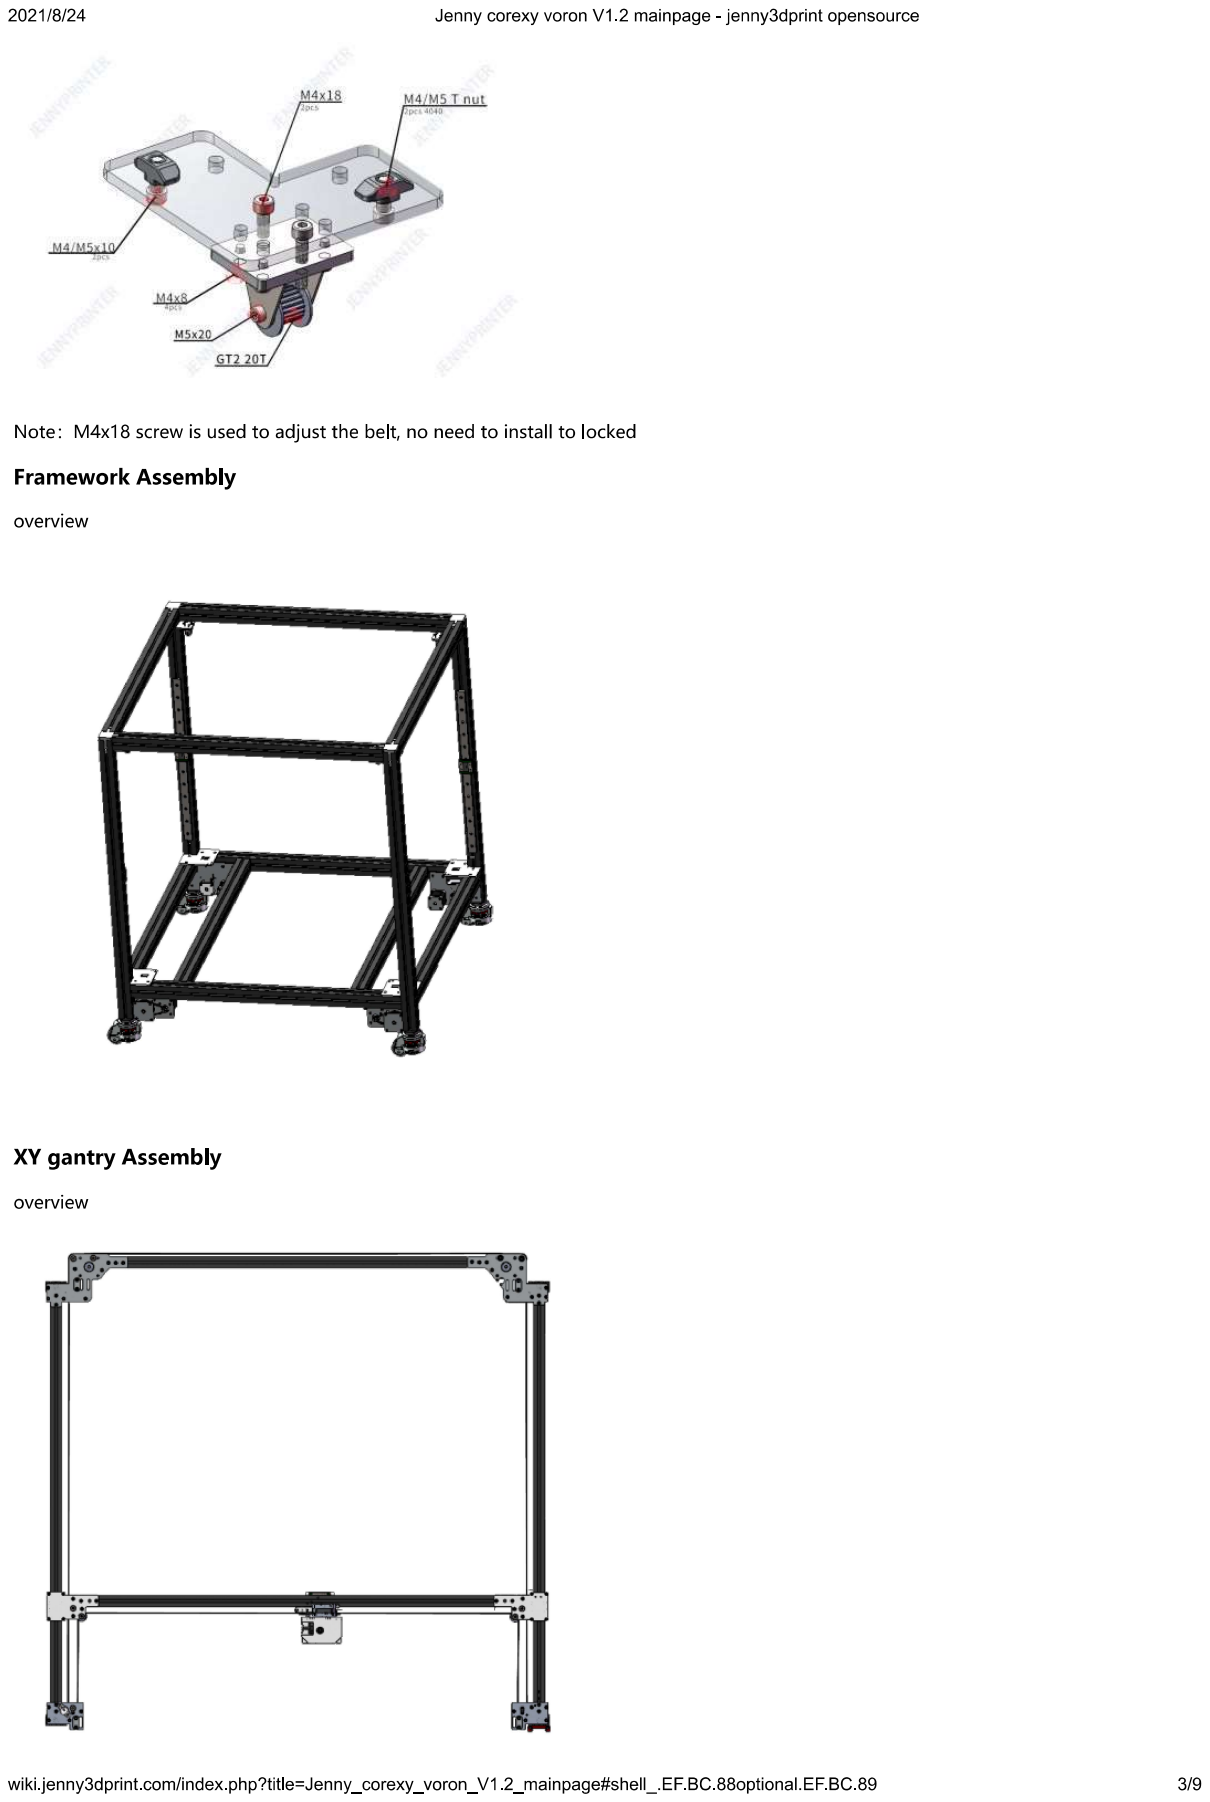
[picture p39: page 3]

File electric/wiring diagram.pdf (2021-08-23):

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

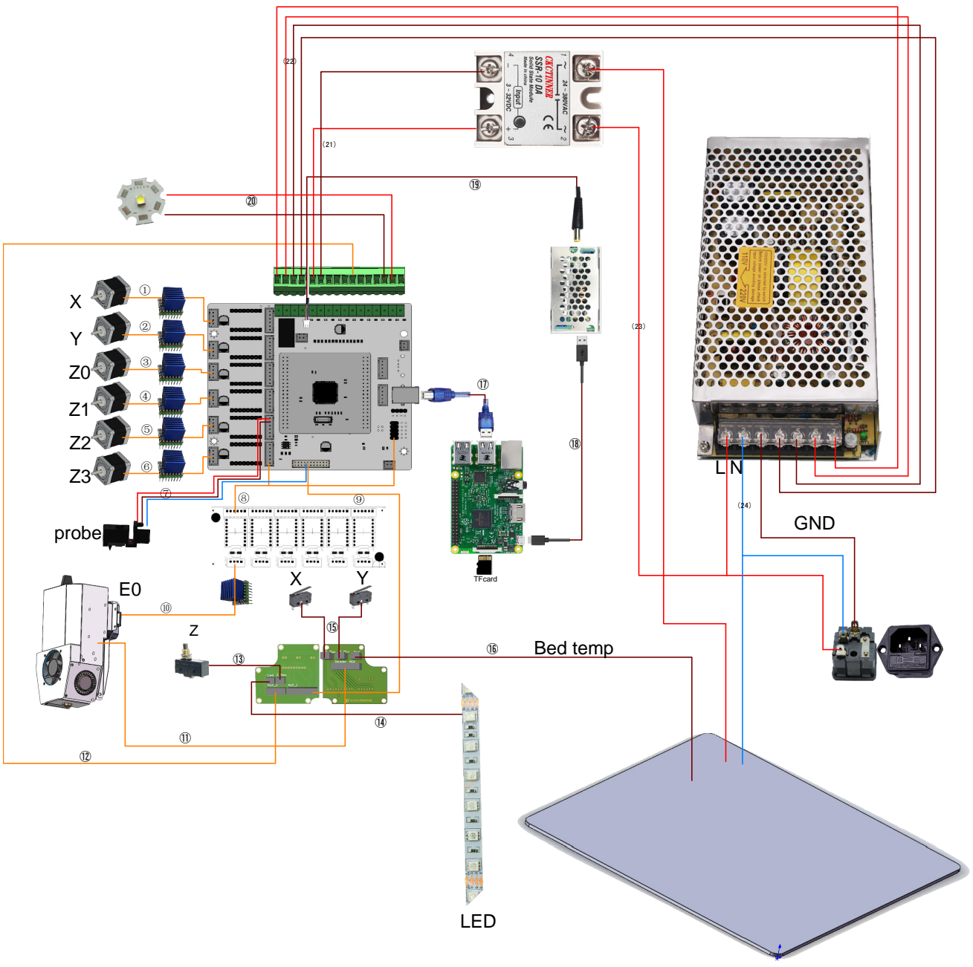
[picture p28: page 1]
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

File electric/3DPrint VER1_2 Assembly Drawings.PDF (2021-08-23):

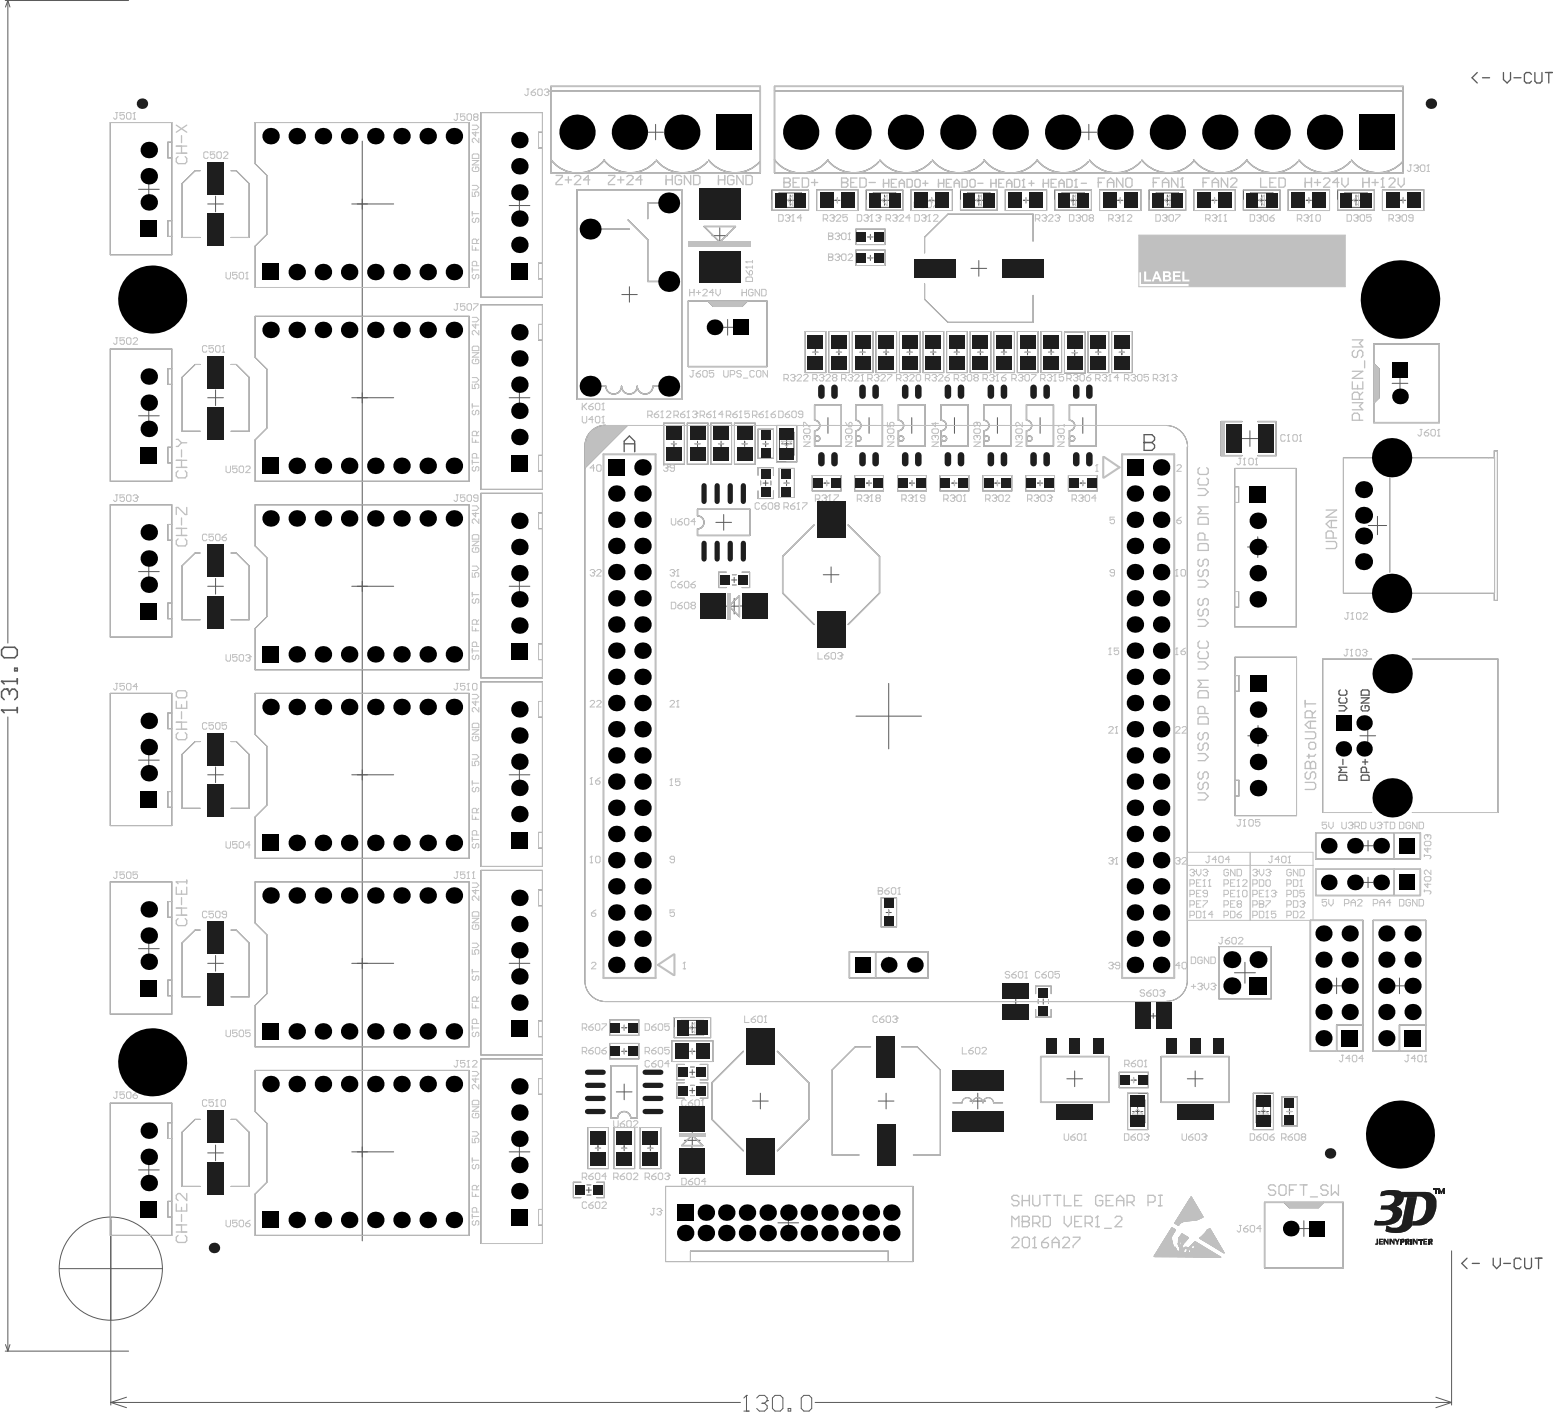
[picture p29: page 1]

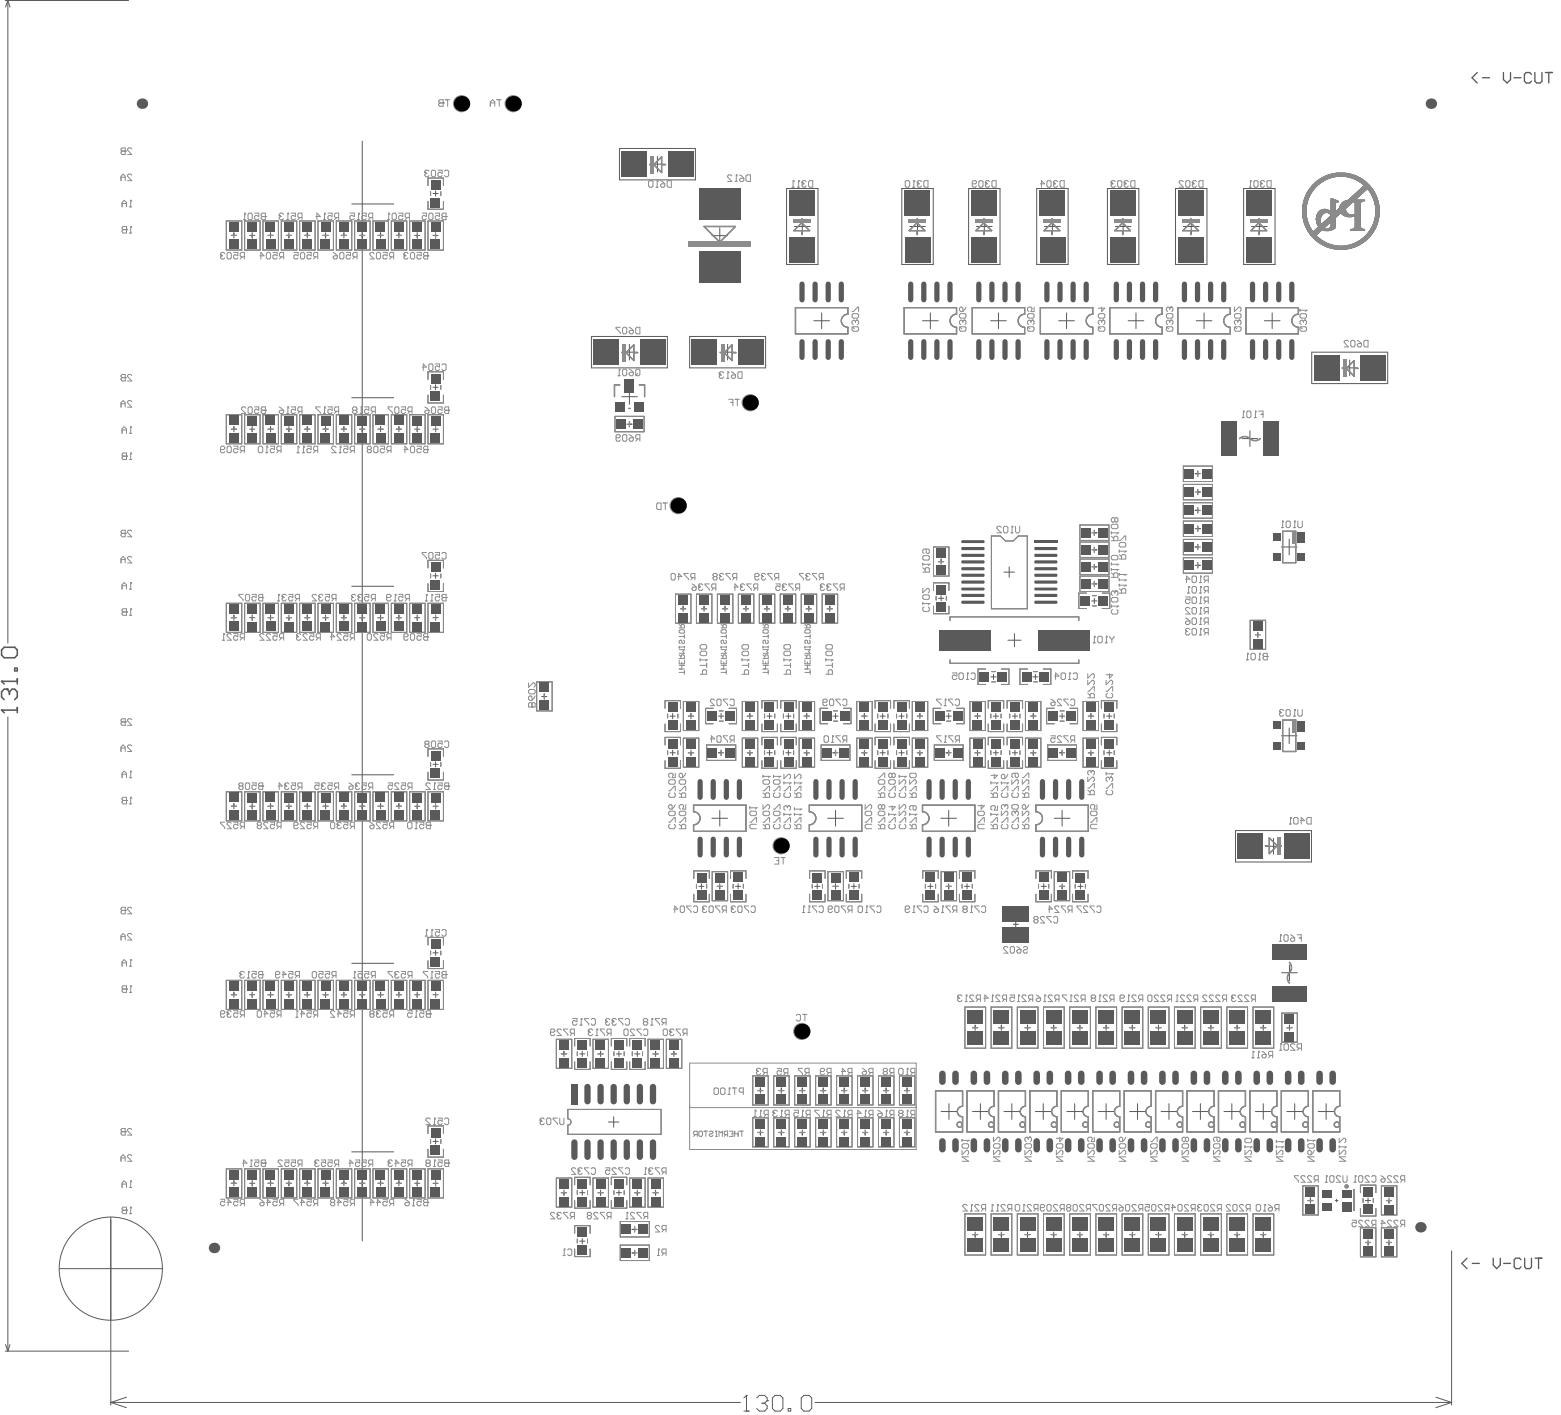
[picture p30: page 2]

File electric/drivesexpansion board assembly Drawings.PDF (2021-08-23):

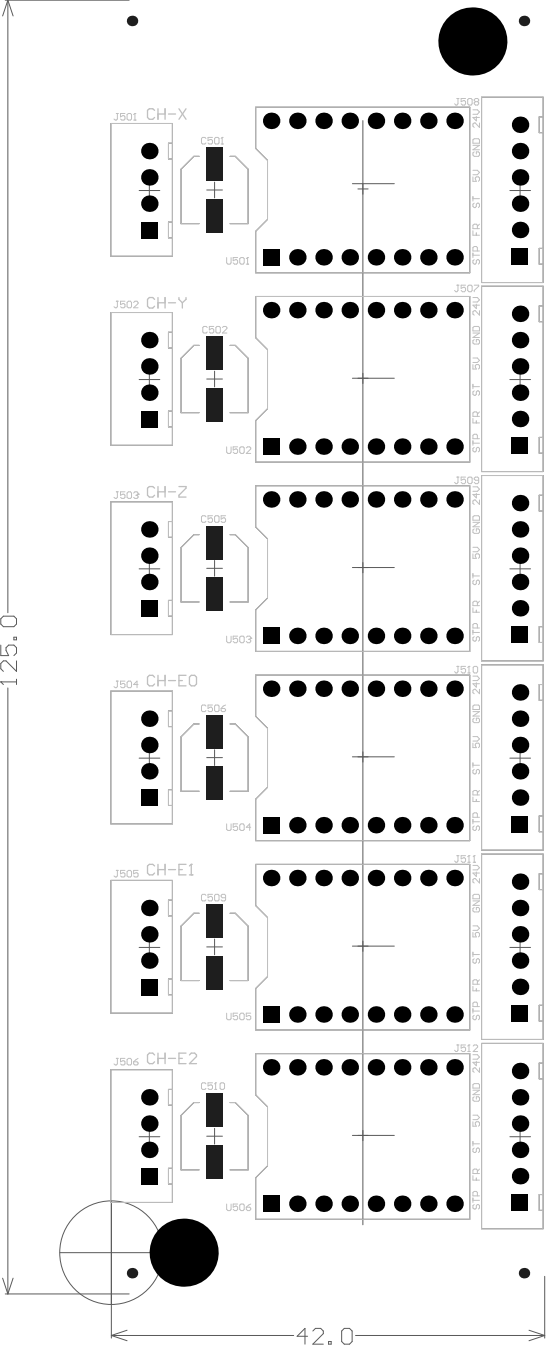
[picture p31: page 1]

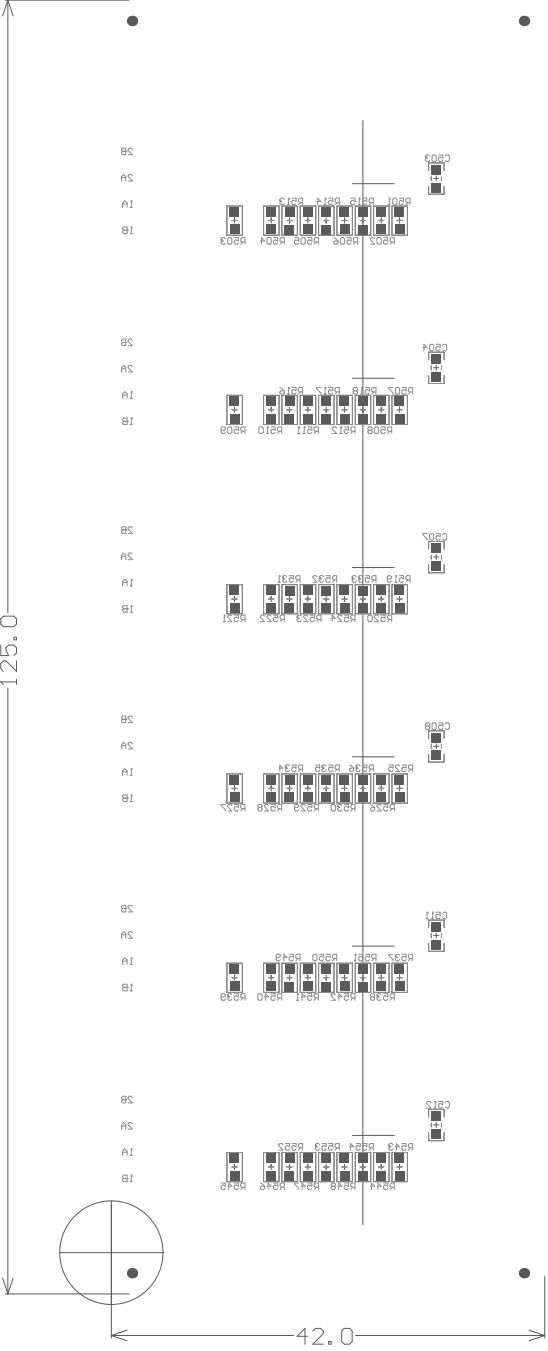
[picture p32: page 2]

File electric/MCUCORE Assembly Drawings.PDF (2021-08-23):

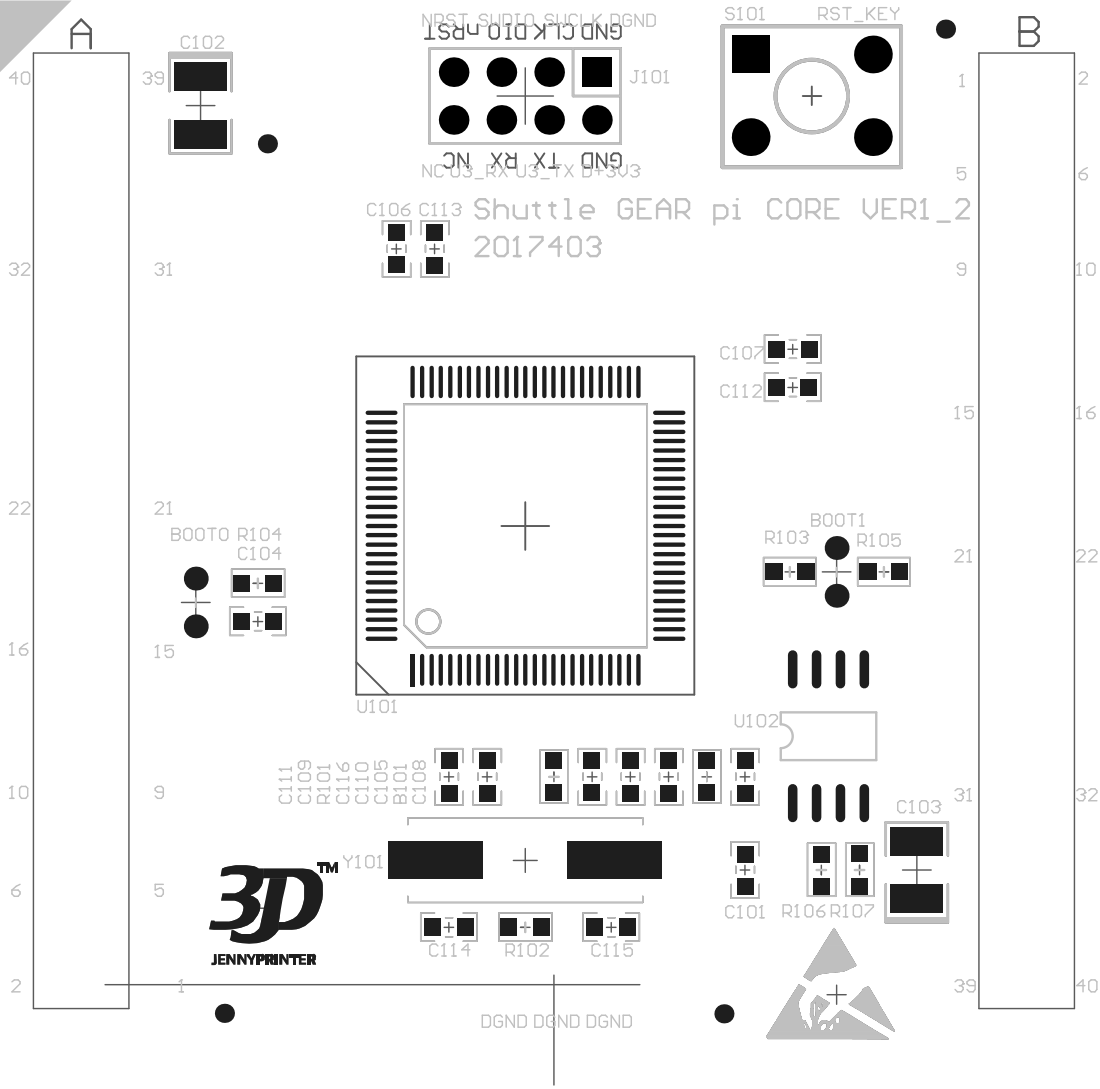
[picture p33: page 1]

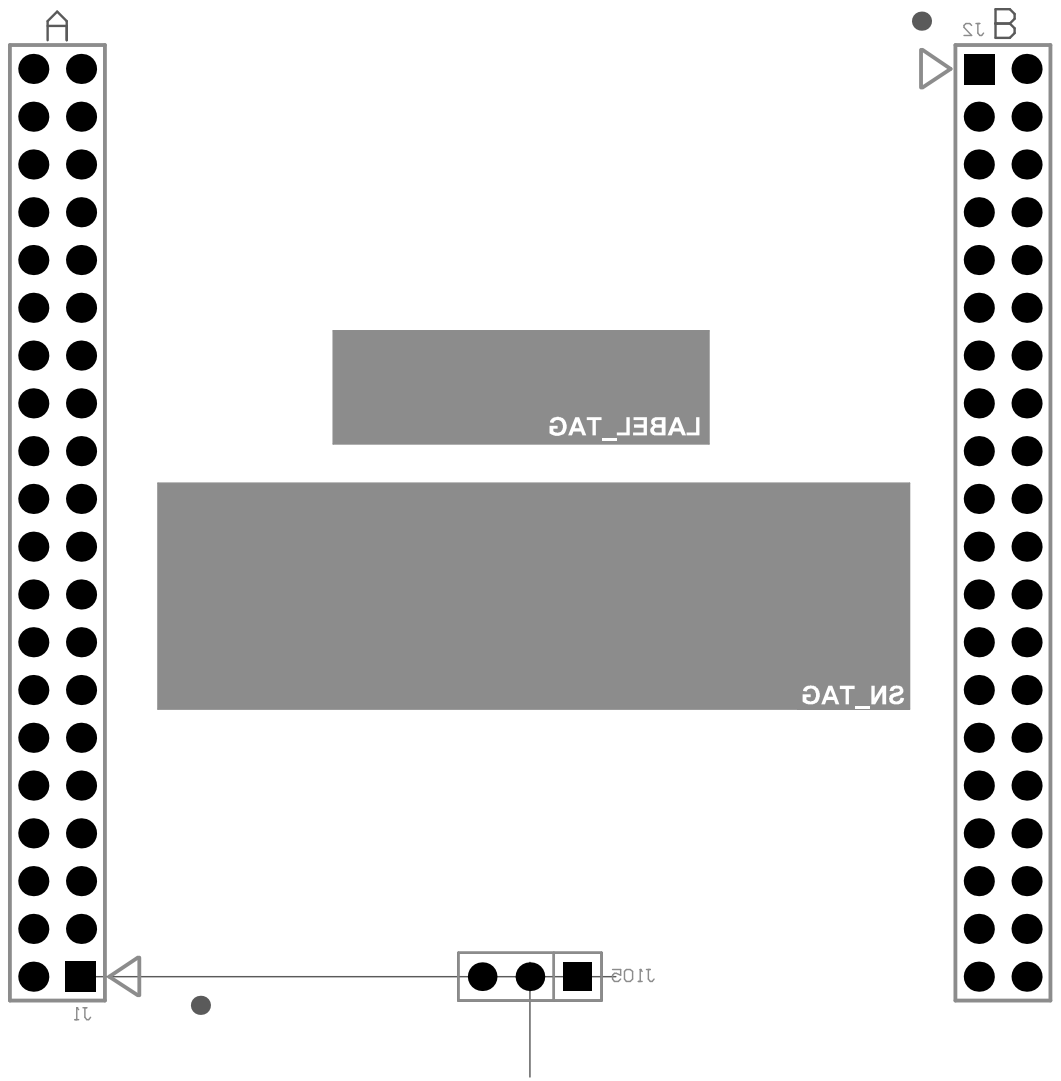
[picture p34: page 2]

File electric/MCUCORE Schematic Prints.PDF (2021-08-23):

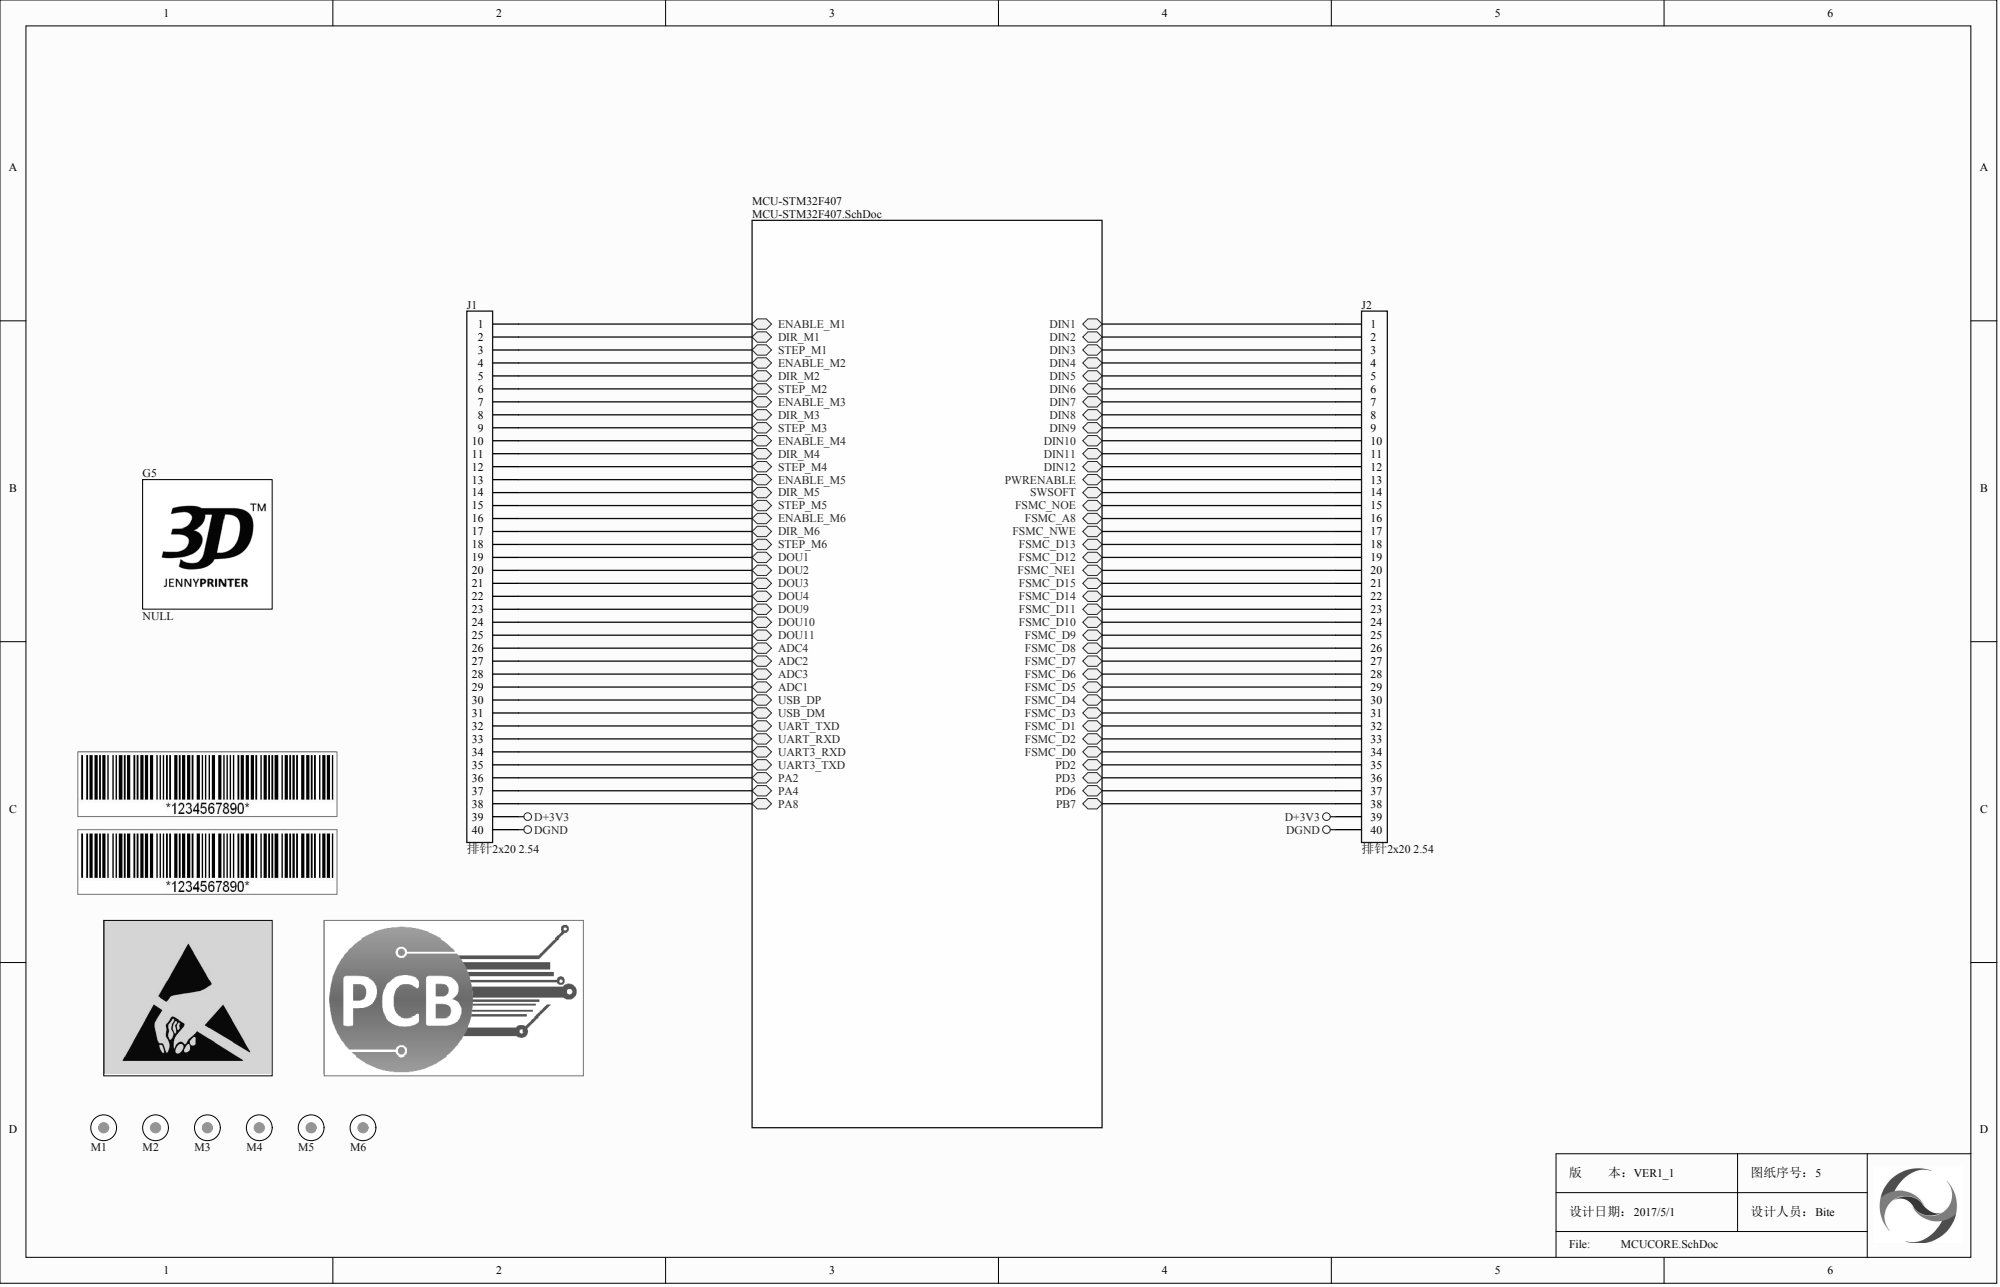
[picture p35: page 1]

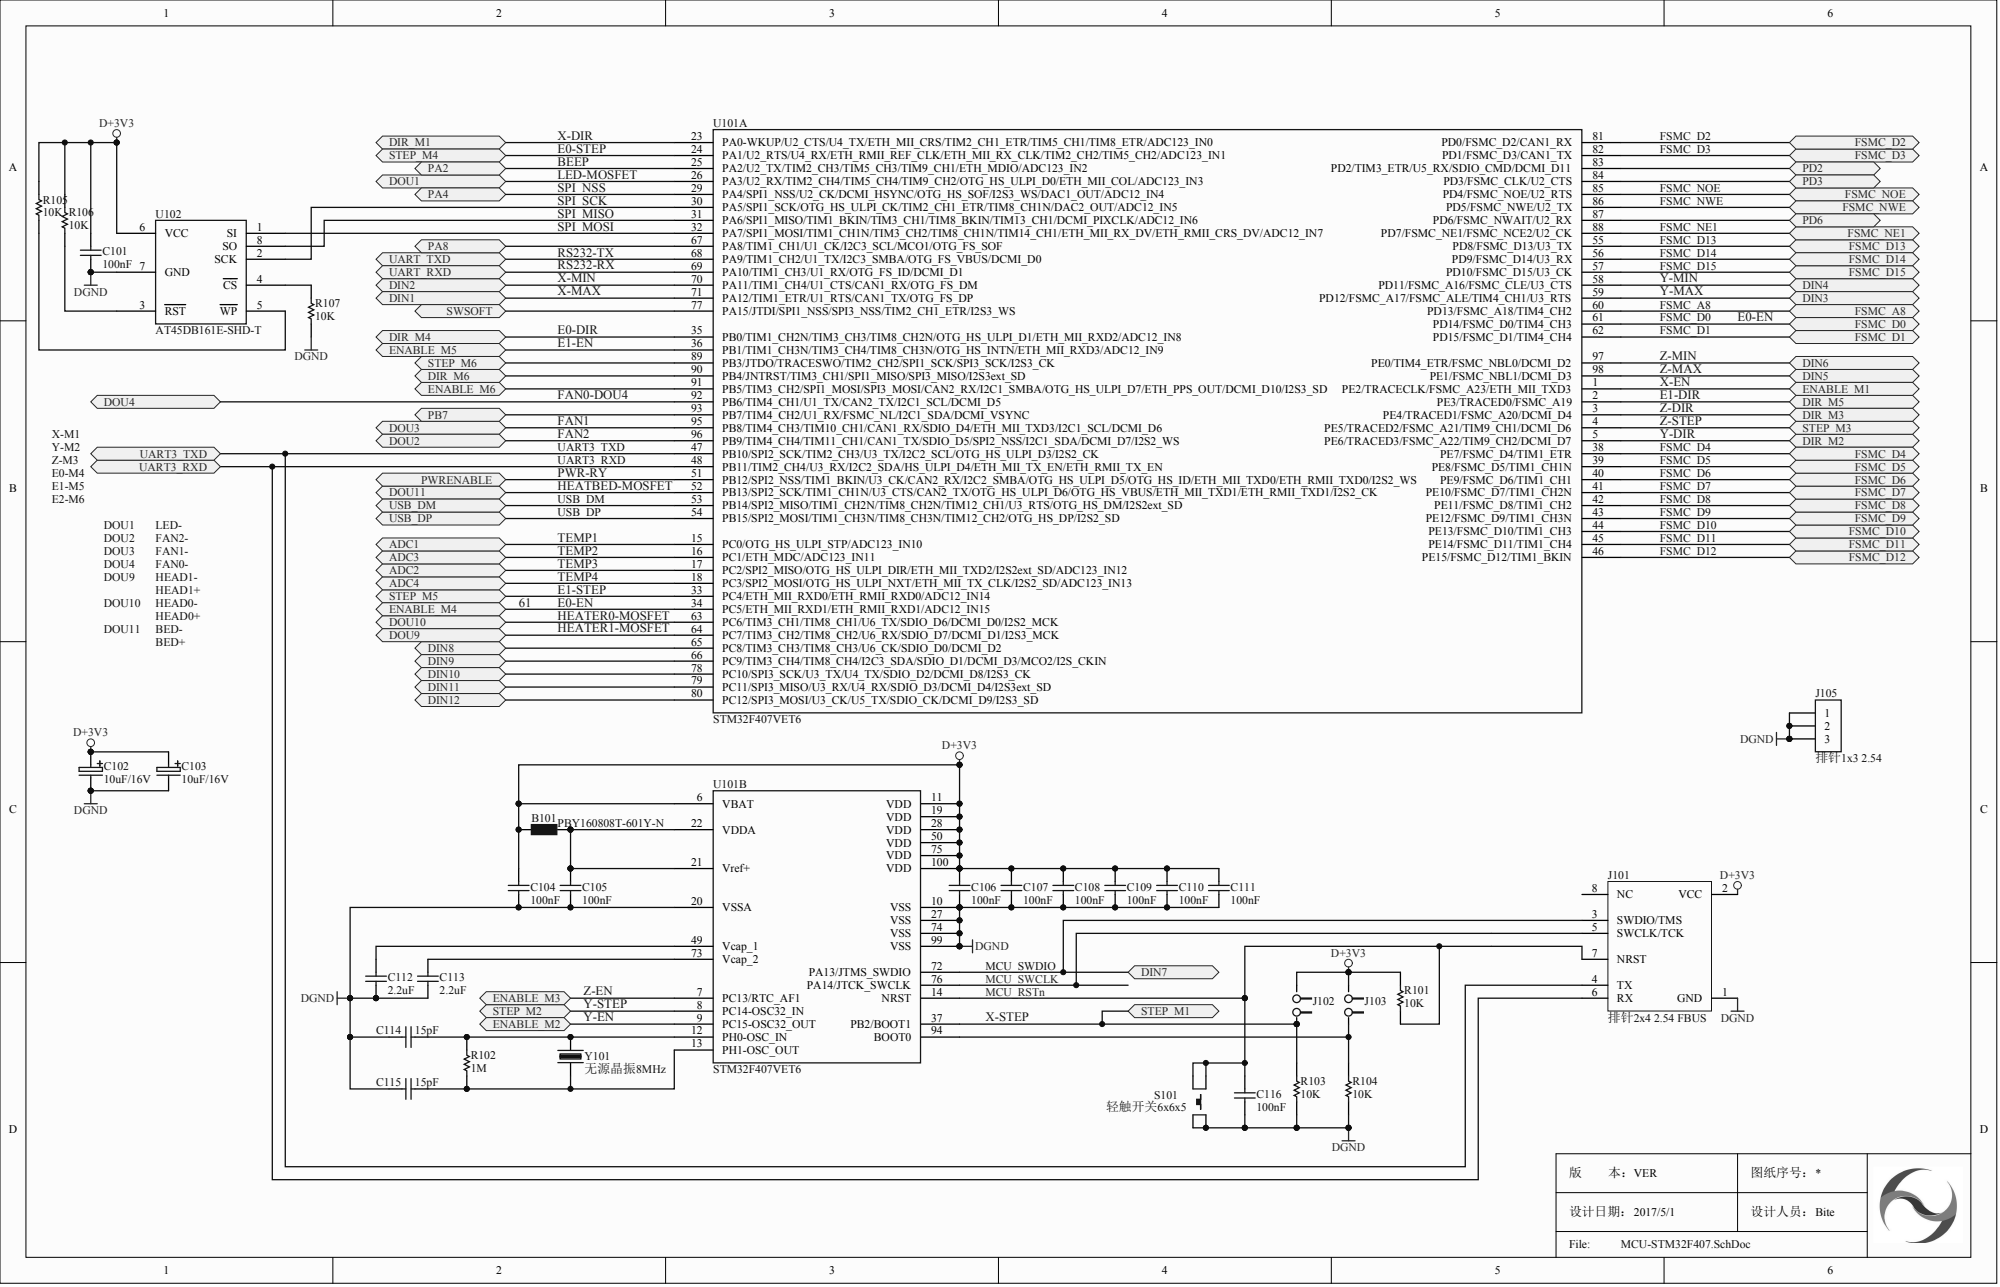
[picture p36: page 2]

MCU_SWCL K
